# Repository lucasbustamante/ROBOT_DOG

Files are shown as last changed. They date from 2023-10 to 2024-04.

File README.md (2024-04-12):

# Robot Dog

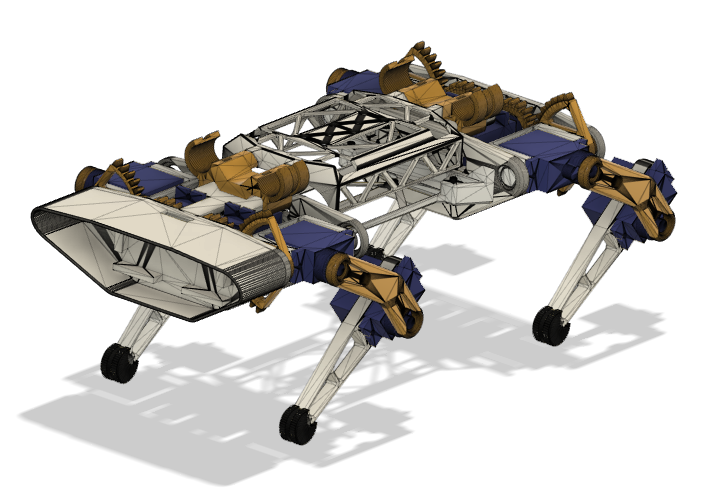
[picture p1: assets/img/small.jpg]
ROBOT_DOG


## Hardware
- ESP32
- MPU9250
- 12 servos TowerPro mg90d
- Baterias 18650
- Mini360
- INA219
- TP4056

## Software
- Compatível com Arduino IDE

## A Fazer

- [x] Criação da PCB
- [x] Alteração do Layout dos Controles
- [x] Melhorias na modelagem 3D
- [x] Impressão 3D
- [x] Montagem da Estrutura
- [x] Implementar sensor de energia INA219
- [ ] Implementar sensor de giroscópio MPU9250
- [ ] Atualizaçao das bibliotecas

## Como Fazer
### Esquema de ligação PCB

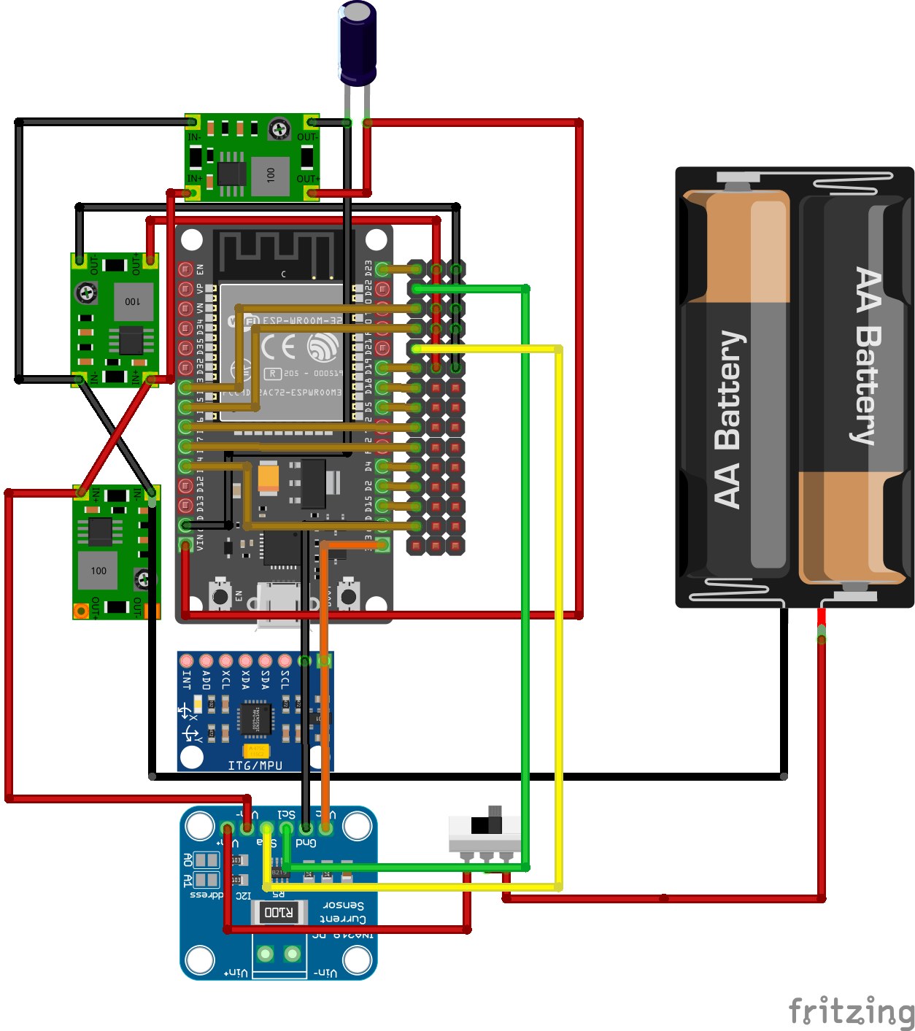
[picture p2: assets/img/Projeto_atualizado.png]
PCB


### Calibrar os servos (criar `servoMainProfile`)
- Imprima a ferramenta `calibrador do servo` e instale o servo nela: um prato circular com pontos, 10 graus cada um de 0 a 180.
- Use a ferramenta `tools/servoCalib.ino` e conecte o servo ao pino 14.
- Abra o terminal do Arduino IDE e digite `1500` (e pressione Enter) - isso deve ser o meio do servo e ele deve apontar para o ponto médio da ferramenta impressa.
- Diminua o valor para encontrar os valores `minAngle` e `degMin` (comece com `800` e diminua até o servo parar de se mover).
- Faça o mesmo para encontrar `maxAngle` e `degMax`, mas comece com 2100 e aumente os valores.
- Ótimo, agora sabemos os limites do nosso servo (ou pelo menos quais são os limites para a lib+servo), hora de encontrar posições mais precisas do servo.
- Insira valores até encontrar as posições adequadas para deg30, deg50...deg130, deg150.

### Conexão
#### Credenciais do ponto de acesso WiFi
- Renomeie config_wifi.example.h para config_wifi.h
- Mude APssid para qualquer nome do seu robô, por exemplo, SmallRobotDog
- Altere APpass para senha (8 ou mais caracteres), por exemplo MySup3rPassw0rd

- Após o upload do código para o ESP32, você poderá encontrar o SmallRobotDog WiFi com seu telefone ou tablet.
- Abra o navegador e insira o URL http://192.168.4.1/ e você verá dois joysticks virtuais para controlar o cão-robô.

### Pernas
#### Montagem
- Para montar as pernas corretamente, imprima a ferramenta `calibrador esq e dir` de calibração de perna para os ângulos Beta e Gamma, assim como a ferramenta `calibrador` de ângulo Alpha.
- Ligue o servo e conecte o ESP32 ao seu computador, abra o terminal do Arduino IDE e faça upload do código principal.
- Digite `set servo_to_calib` para definir todos os servos na posição esperada para a ferramenta de impressão.
- Monte as pernas o mais próximo possível das posições esperadas das partes da perna de acordo com a ferramenta (90 graus, 45 graus, 90 graus).

#### Calibração
- Repita os passos 2 e 3 da instrução Pernas->Montagem.
- Digite `set help` para ver a lista de comandos disponíveis, estamos interessados em `XX_HAL_trim_xxxx`, por exemplo, `LF_HAL_trim_alpha`, onde `LF` - perna frontal esquerda, e `alpha` é o nome do ângulo.
- Coloque a ferramenta de ângulo Alpha em cima dos servos das pernas do robô, a superfície da ferramenta deve estar (quase) perfeitamente alinhada com o corpo dos servos, se não estiver, use o comando `XX_HAL_trim_alpha valor_em_graus` para definir o valor de ajuste do servo, por exemplo, `set LF_HAL_trim_alpha -3`, não deve ser muito grande, em outros casos você precisa repetir o passo de Montagem.
- Usando a ferramenta para os ângulos Beta e Gamma, calibre/ajuste os outros servos.

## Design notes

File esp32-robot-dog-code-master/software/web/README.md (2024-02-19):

# Interface de Controle

## Alterar a Interface
(Este procedimento foi testado apenas em sistemas Linux)

Para alterar a interface de controle, siga as etapas abaixo:

1. Localize o arquivo **index.html** no seguinte caminho: `/esp32-robot-dog-code-master/software/web/src`.

2. Após efetuar as alterações necessárias, você precisará converter este arquivo HTML para os formatos **.gz** e **.gz.h**.

3. Agora, abra o terminal e navegue até o seguinte caminho: `/esp32-robot-dog-code-master/software/web`.

4. Execute os seguintes comandos:
   (use a versão 12 ou inferior do Node.js)
   - `npm install`: Isso instalará os pacotes do Node.js necessários.
   - `gulp`: Este comando irá compilar a interface web.

5. O arquivo resultante estará disponível na pasta **web** do projeto.

Agora você concluiu o processo de geração da nova interface com sucesso.

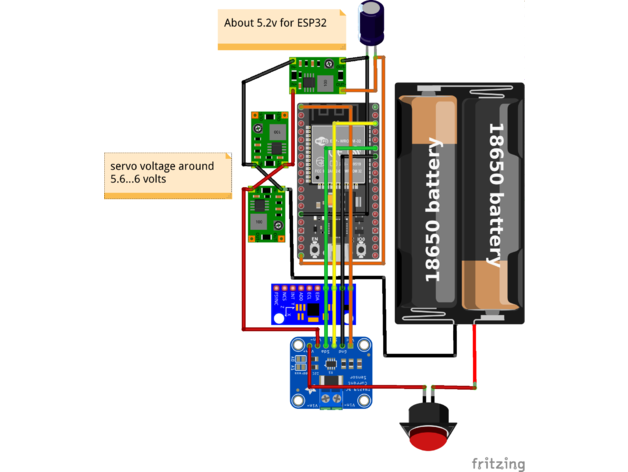
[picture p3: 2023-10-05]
Modelo 3D/images/featured_preview_scheme_power_and_sensors.png

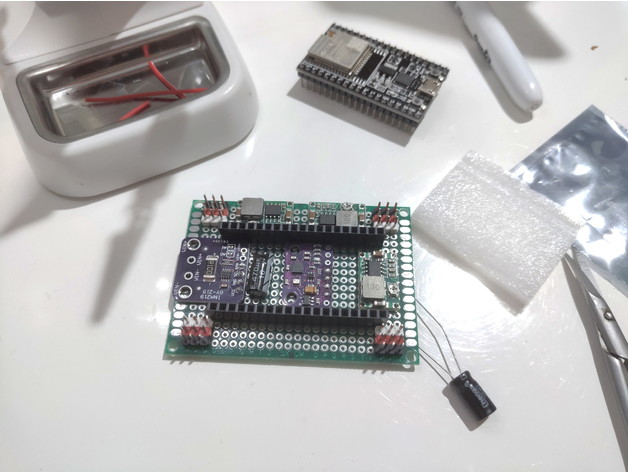
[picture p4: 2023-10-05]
Modelo 3D/images/featured_preview_2021-03-04_20.57.48.jpg

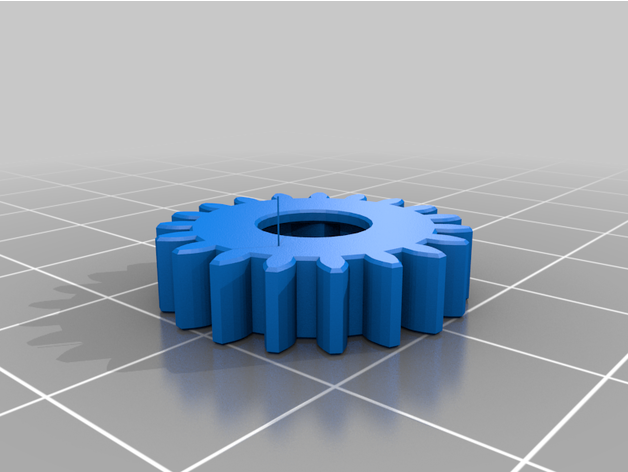
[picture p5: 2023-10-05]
Modelo 3D/images/servo_gear.png

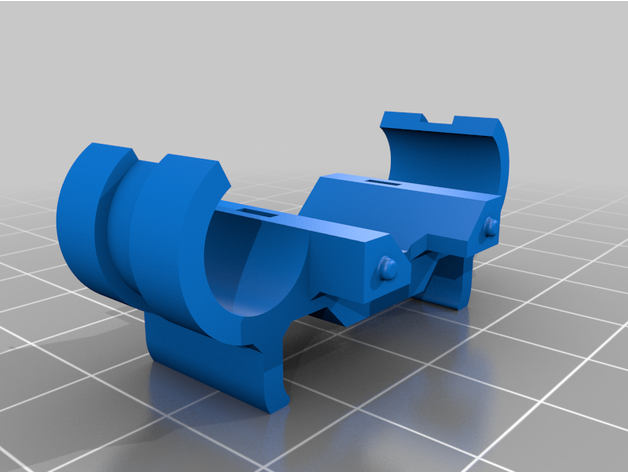
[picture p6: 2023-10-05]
Modelo 3D/images/cover_clamp.png

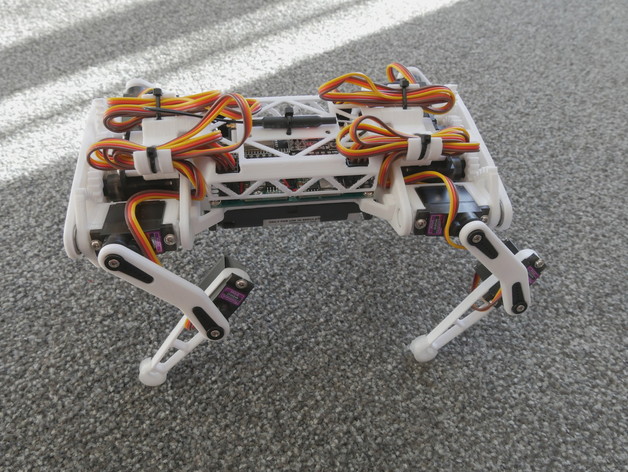
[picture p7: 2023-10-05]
Modelo 3D/images/featured_preview_2.JPG

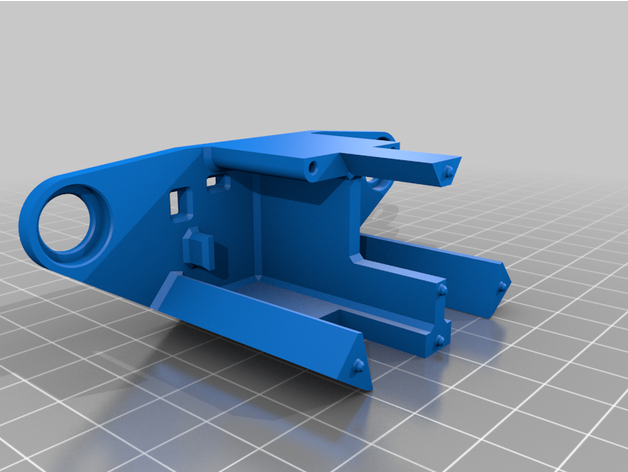
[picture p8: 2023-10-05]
Modelo 3D/images/legs_holder_part1.png

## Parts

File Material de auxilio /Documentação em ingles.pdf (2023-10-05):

instructables

## ESP32 Small Robot Dog (closed) (http://www.instructables.com/ESP32-Small-Robot-Dog/)

by Gleb Devyatkin (http://www.instructables.com/member/Gleb+Devyatkin/)

### Disclaimer

This project has been done mostly for fun about a year ago. Some libraries have been updated, so it basically does not work any more. Not every planned feature was released. No PCB is made and it creates a lot of trouble for most of you. I'm sorry to say, but I'm not going to provide any support for it any more. It's exhausting and sometimes just destroys any intentions to continue. This is not commercial project and I'm not going to do something like Donation. Maybe I'm disappointing someone. Sorry. Project closed.

ESP32 small robot dog is my attempt to make quadruped dog that become very popular after Boston Dynamics Spot. Work on the project still in progress and hardware and software can changed.

### Features

### Only ESP32 required (you don't need additional PWM i2c, Bluetooth modules, etc) Arduino IDE

Web based interface with telemetry, to control robot you will need just you smartphone or tablet

### CLI interface for calibration and debug True Inverse kinematics code Con0gurable Gait sequence and settings (just if you need it) Fun

### Electronics

### 1 x ESP32 with 38pin 1 x 50x70 mm green prototyping board

12 x TowerPro MG90D or MD90S (cable should be out at the bottom of servo, thanks to triawan) (https://www.thingiverse.com/make:942053) servos (it can be tricky to use other servos, as size may vary, please have a look at this images of three di9erent

### mg90-like servos: https://www.instagram.com/p/COoIyvzrLZt/) 1 x INA219 (optional) 1 x MPU9250 (optional, still has not been implemented, WIP)

3 x Mini360 (DC-DC Buck Converter Step Down Module) or similar, 2 for front/hind legs (or more), 1 for

### ESP32 1 x 18650 Battery Holder for 2 elements (try to 0nd "18650 battery holder smt") 2 x 18650 Battery some capacitors

### Other parts

ESP32 Small Robot Dog (closed): Page 1

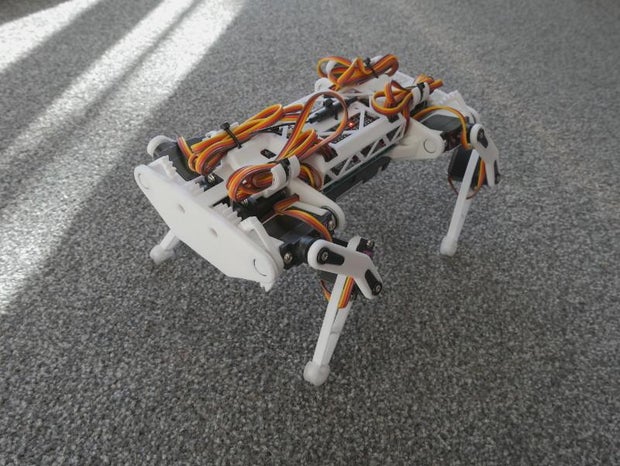
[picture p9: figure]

Step 1: Print Parts

### 8 x 8x12x2.5mm bearings 4 x small cable ties Super glue (cyanoacrylate) to glue all parts together

https://www.youtube.com/watch?v=jzs04zd9bQk

All STLs to print can be downloaded from Thingiverse page: Robot dog, quadruped robot, 12DOF, 3DOF per leg (https://www.thingiverse.com/thing:4822059)
Some part should be mirrored to be able to print correctly. Please see attached images.
My printer have issue with 0rst layer thickness, aka Elephant Foot. Gears should be printed as perfect as possible, so I add very tiny spacer to avoid issue, you will see that some part "Eying" over surface, so please enable support for it.
I'm strongly recommend print parts with best possible quality, especially gears. As also use brim and ironing.

### Full list of parts to print: Printable parts: 1 x Body

### 2 x Leg top 2 x Leg top (mirrored) 2 x Leg bottom 2 x Leg bottom (mirrored) 4 x Shoulder part1 4 x Shoulder part2 2 x Legs holder part1 2 x Legs holder part2 4 x Servo gear 4 x Leg shoes, print with Eexible 0lament (not required) 1 x Cover 2 x Cover clamps

Printable helping tools (see description on GitHub): (https://github.com/SovGVD/esp32-robot-dog-code)

### 1. 1 x CALIBRATION_LEG-Beta_and_Gamma 2. 1 x CALIBRATION_LEG-Beta_and_Gamma (mirrored) 3. 1 x CALIBRATION_LEG-Alpha 4. 1 x CALIBRATION_SERVO-10deg

I'm using Ender 3 Pro, Cura, use Support and choose Dynamic quality. Plastic is PLA from OPY (AliExpress). For more

### details please visit Thingiverse page: https://www.thingiverse.com/thing:4822059

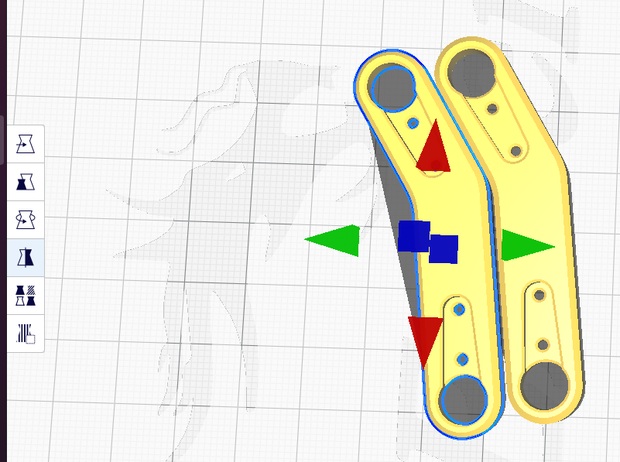
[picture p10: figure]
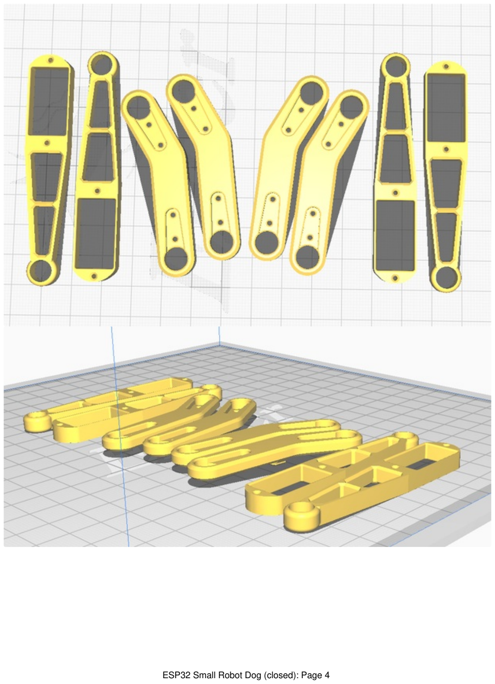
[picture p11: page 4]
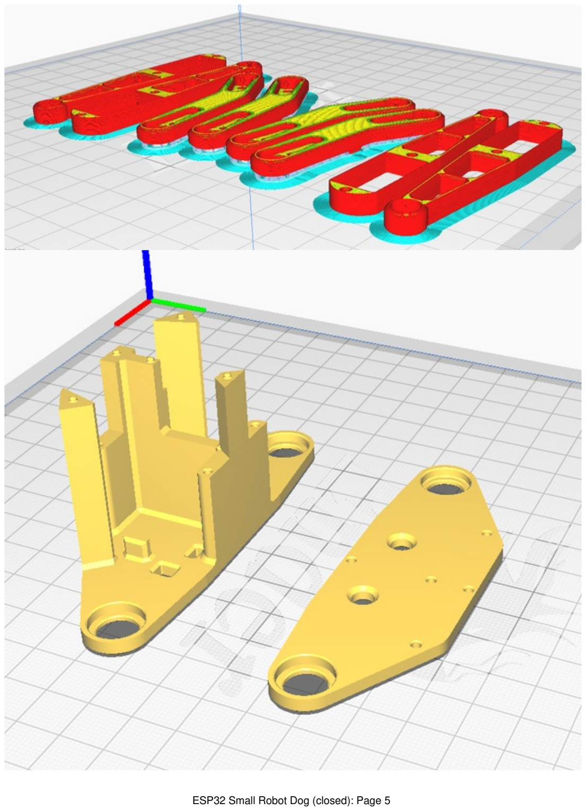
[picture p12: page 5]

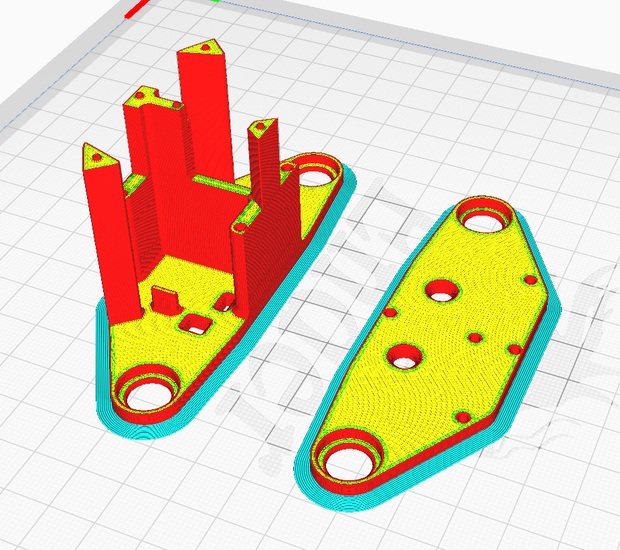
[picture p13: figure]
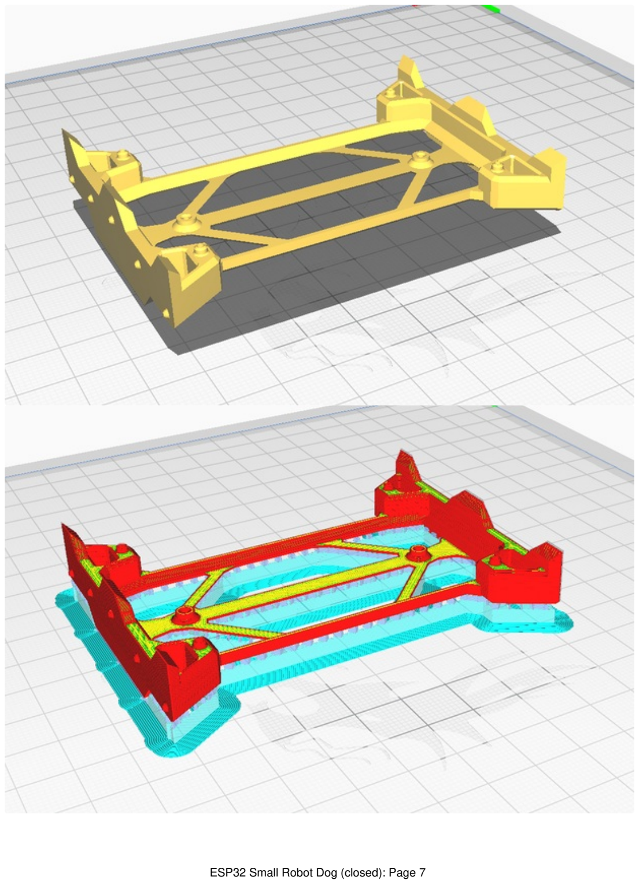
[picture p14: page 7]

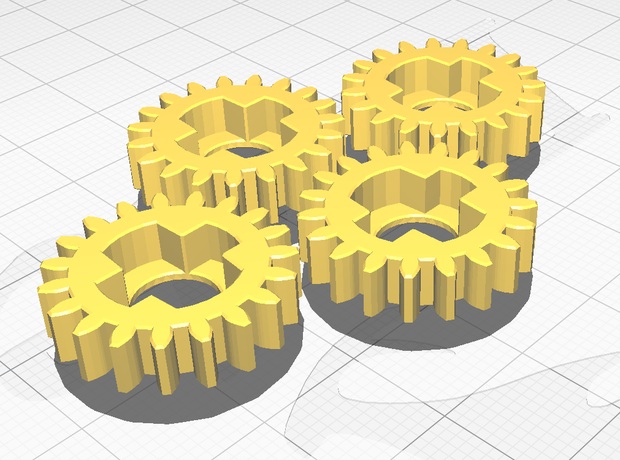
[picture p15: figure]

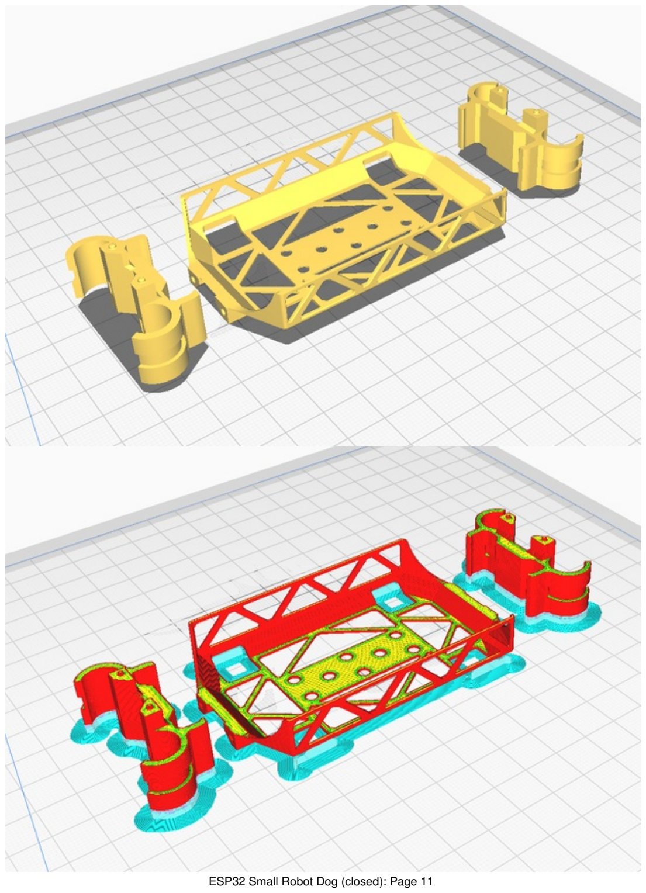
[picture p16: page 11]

Step 2: Let's Make It Better and Glue Together

### Preparation

Before we start, please check that bearings can be easy 0t to body parts and over shoulder parts.
Also check that holes in Shoulder and body parts printed 0ne and servo cables (temporary disassemble servo connector) can be 0t inside.

### Do it

I tried to make body as light as possible, as small servos not very powerful. That is why you will need to glue some parts

### together. Promise it is not so hard =)

Make sure that gluing surfaces are Eat, use some Eat mini 0le and make sure parts can be connected to each other without space between. Then glue it together as shown on images.

### Servo gears

Cut servo horn (see image) to 0t it inside servo gear part and glue it together.





Step 3: Legs

Glue short servo horns into "leg top" parts.
Insert servo into "leg bottom part" and insert cable as shown on image. Pull another servo cable through one of the hole on the "shoulder" part. Repeat with other legs.





Step 4: Assemble Body and Legs Together

As was shown on previous pictures, pull all cables through legs and body holes.
Set all servos to middle using Arduino/ESP32 or servo tester.
Cut servo horn to make it 0t inside "servo gear", glue it and install on the servo as usual. Insert servos into body. Screwing it can be challenging.
Squeeze "shoulder" part without servo (but with cable in place) and insert it between bearings.
Repeat with other servos and parts.
You don't need to 0x legs with bolts at that moment, later you will need to calibrate legs following instruction in my

### GitHub repository: https://github.com/SovGVD/esp32-robot-dog-code





Step 5: PCB

PCB con0guration is up to you. I can only show what I did. Sensors connected to default I2C bus of ESP32 (GPIO 21 and 22).

### Servos connected to:

Left front: 25 (body servo, servo gear, alpha), 26 (body to leg servo, shoulder, beta), 27 (leg servo,gamma)

### Right front: 16, 18, 17 Left hind (back): 13, 12, 14 Right hind (back): 4, 2, 15

You can recon0gure it in the code, but make sure that ESP32 ISR Servo library (https://github.com/khoih-prog/ESP32_ISR_Servo/) support it.





Thank you for all the effort you put into this. I built it but I did have problems soldering up the board, as others did apparently, so I decided to create a pcb instead. If you reboot this project and would like me to upload my gerber files let me know.

I would definitely appreciate some PCB files being posted- I tried soldering one up but my parts aren't exactly the same as his so the arrangement is different, so my pcb is a mess of wires and is extremely difficult to troubleshoot. Thanks in advance!

I also had a heck of time wiring up the circuit. I thought it was me but apparently others have also found it quite challenging. After two failed attempts at laying out and soldering up the board I decided to try creating a pcb using Fritzing. I did it and sent it out to Aisler to be printed. The board looks good but I haven't tried to use it so I can't say if it actually works or not. Unfortunately it seems I'm not allowed to updoad zip files or the gerber file types so I've uploaded my Fritzing circuit file and a pdf of it. Good luck!

Thanks! I ended up designing my own PCB based on the schematic since I wanted to use the IMU, but I appreciate the help. Fritzing’s autoroute feature really is a lifesaver.

Perfect!

Step 6: Code
Step 7: Good Luck!

Setup Arduino IDE to work with ESP32 (https://randomnerdtutorials.com/installing-the-esp32-board-in-arduino-ide-windows-instructions/) but don't use esp32 version 2 and higher. There were some strange changes

### related to WiFi, so one of the core just freezing in v2.x.x

Install addition libraries (most of them could be installed in Arduino IDE "Sketch" menu -> "Include Library" -> "Manage

### Libraries...", please use only specied version):

ESP Async Web Server (https://github.com/me-no-dev/ESPAsyncWebServer) with Async TCP (https://github.com/me-no-dev/AsyncTCP) ESP32 ISR Servo (https://github.com/khoih-prog/ESP32_ISR_Servo#use-arduino-library-manager) version 1.1.0

### MPU9250_WE (https://github.com/wollewald/MPU9250_WE) version 1.1.3 INA219_WE (https://github.com/wollewald/INA219_WE)

Setup WiFi Access point credentials.

### 1. Rename con0g_wi0.example.h to con0g_wi0.h 2. Change APssid to any name of your robot, e.g. SmallRobotDog 3. Change APpass to password (8 or more chars), e.g. MySup3rPassw0rd

4. After code upload to ESP32 you should be able to 0nd SmallRobotDog WiFi with your phone or tablet.

Open browser and input URL http://192.168.4.1/ and you will see two virtual joystick to control robot dog.

Hope you like that project. More code and instruction updates on the go and hopefully will be release soon.

I try to compile the code you give but at the end is Hal_PWM is error the arduine IDE wont finish its compile before insert code to Esp32. Any idea how to solve it?

Hi. I just tried this code with newest version of all libraries and found that everything broken =( I've update instruction with versions that at least should compile without errors:
- ESP32 ISR Servo version 1.1.0
- MPU9250_WE version 1.1.3
Version of the library could be chosen in Arduino IDE Library manager in dropdown menu near Install button.
I will try to update code and test it with latest version of library some times later (with the new walking robot). Sorry, just have no time at the moment for that project and did not see anyone going to help with it.

That Library is Good to go. If you want help from me i can help you but I dont know how to start with, im newbie. Now I'm going to build the circuit board. In time I try to connect with My Computer browser it does show up 2 button to control the robot but when I try to using My phone its show the button but can't shake it. I don't know why?

Try another browser. I'm using Android phone with Google Chrome.

goggle browser is now work, the button can move but after Wifi connect to robot when i try to move the button nothing happen. what should i do next?

Did you assemble robot, connect all servos and provide power to it?

Yes I already assemble it.
and power it. All servo had rotation.

I think its lack in my Component, i don't use MPU and INA219 I only power it straight to Esp and servo. Maybe that the reason why it can't move. (The article above is Optional)

MPU and INA should not be the problem. Sorry but I can't test my setup without that sensors. As also can't check code at the moment. Maybe this weekend I will find time for it.

Dear Mr. Gleb
Sorry to bore you, i think I will use Ina and Mpu next. but I already Solve it, it seem my Esp32 Core is corrupted so I Re-Install the library, its work like charm. But when I turn on the Robot all Servo move like crazy, its seems the Servo Pin is not correct, like Pin 16 in Esp32 I cant find the Pin.
I would know all Pin did you use for Servo?

Dear Mr. Gleb
I already figure out about ServoPin, now the robot can move correctly but when I turn on the esp and servo with power, all servo move clockwise and temporary i build 2 switch, 1 for esp and 2 for servo. it seems when power up esp and servo together esp had low voltage and reset the positioning servo but after a few second servo go back to original position. how do you solve this problem?
I too put some capasitor but it does nothing, by the way I use 330uf,
what capacitor did you use?
well another problem to solve

Best Rigard

Hi. You are not the first who have that problem and I can't reproduce it to understand and fix. I'm using mg90d servos.

I will check the Mg90d servo although i use Mg90s,
i think the problem is on trimmer setting on first boot, it say :
0 leg trim (0,0,0)

1 leg trim (0,0,0)
2 leg trim
3 leg trim
but when we find place where to adjust, the problem will solve.
need time to learn,

Hi, great design, thanks! One question about the servos, you say MG90D or MG90S, will the MG90S fit properly? Someone on Instagram said it didn't fit.

its Fit for Mg90s Servo. I try it already.
if not in 3D setting or Printer type the tolerrance is big.

Hi i saw in photos that you connect something to vin+ and vin- but you didnt show in pcb layout

Hi, ina219 module have 2 pairs of vin+ and vin-. On scheme it is connected to pins near i2c data pins.

To ina 219

İf you cant find ESP Async Web Server in arduino libraries you should download this libraries to arduino https://github.com/me-no-dev/ESPAsyncTCPhttps://github.com/me-no-dev/ESPAsyncWebServer
these two libraries literally solve my problems. Thanks to Gleb Devyatkin

Yes, that two, sorry for delay with reply. I add links to libraries.

hello sir

Hello

how did you connect the inner servos to the gears? i dont see that in your instructions. Please assist. Thank you

Updated. You need to cut one of the servo horns to make it fit inside printed gear. Use glue.

Thanks thats what I thought but just wanted to be certain.

Am I missing the PCB layout? Please post it too or a link on how to put all the electronics togeter.

In step 5 you can find scheme of connection for most of parts, as also list of pins for servos. It is not properly made PCB, just connections.

What is the spec for the capacitor and what is it for?

I think it's not required for that project. I used to use a couple of capacitors in another project, where start of DC motor take too much power for a very short period of time, so capacitor save controller from poweroff at the start.

well, its in your photos and on the drawing. therefore I was asking.

Looks cool. Can it already walk too?

It can walk.

This looks amazing! How much is the estimated cost of parts? Except the 3D printer of course.

Sorry, I did not count the final cost. And it will be very different depends on shops with electronic parts or delivery price. Everything (including fillament for 3D printer) bought on Aliexpress.

Well this looks totally amazing, well done. I hope you continue developing it. I'm amazed how good it is with standard small servos. Maybe next one will be bigger and use stepper motors now you've proved the concept.

Thank you. New features in progress. I made this small robot dog to easy test code and algorithms for the bigger version (also servo based): https://www.instagram.com/p/CDX-HhODbw4/ (https://www.instagram.com/p/CDX-HhODbw4/)

amazing!

Awesome!

Very nice work! : )

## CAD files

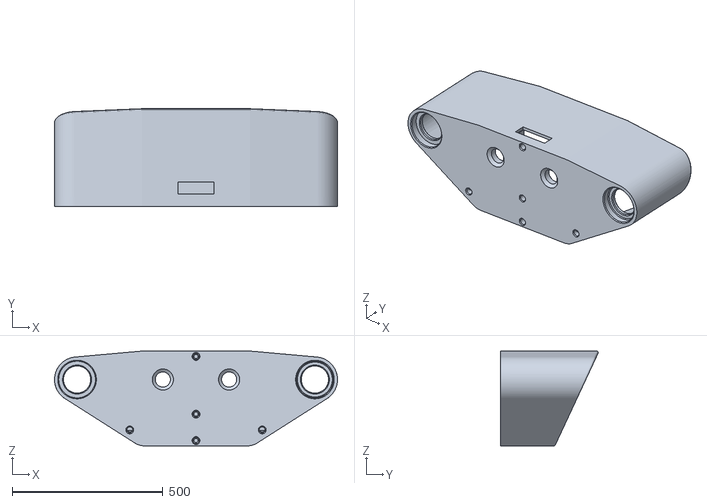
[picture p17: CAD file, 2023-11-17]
Modelo 3D/files/suporte perna part2 v1.stl
940.0 x 324.1 x 315.1

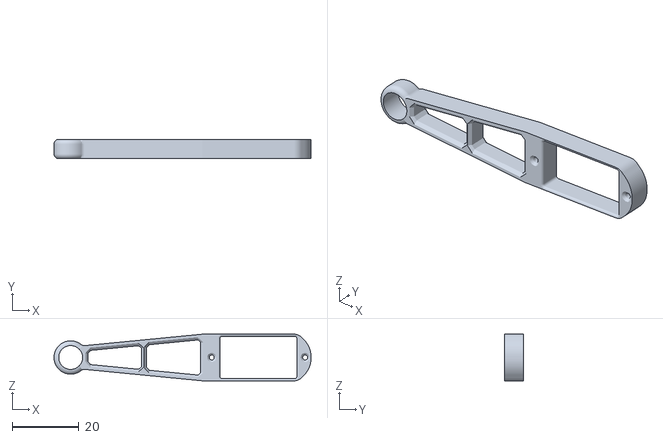
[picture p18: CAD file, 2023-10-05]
Modelo 3D/files/pata.stl
77.0 x 5.80 x 14.0

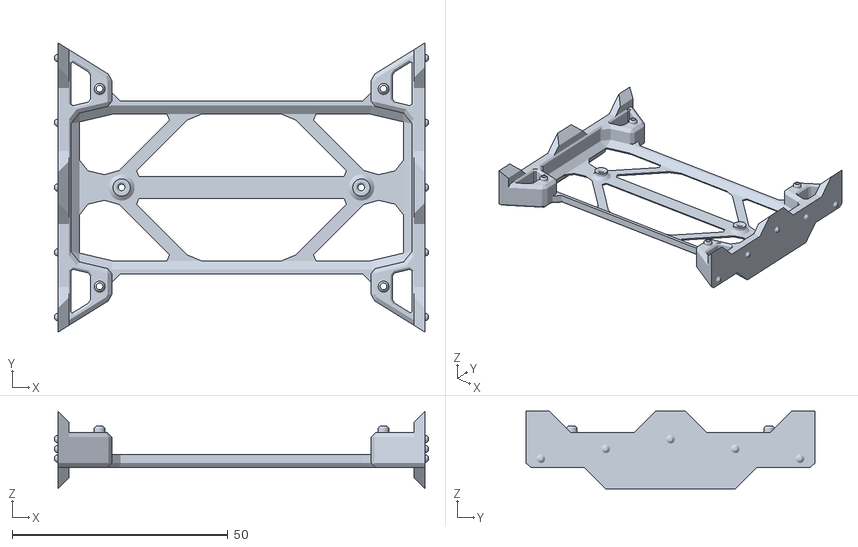
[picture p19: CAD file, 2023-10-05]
Modelo 3D/files/corpo.stl
86.6 x 67.0 x 18.0

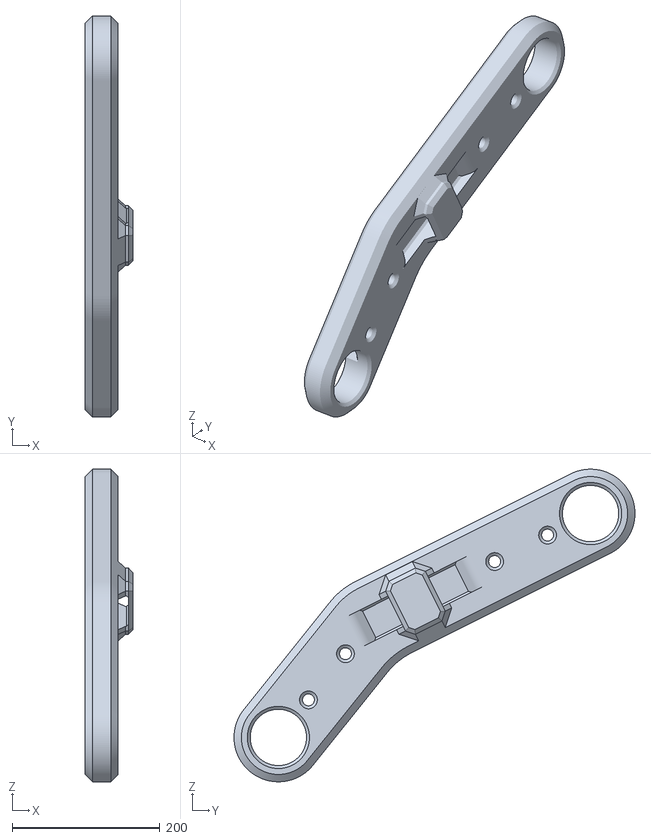
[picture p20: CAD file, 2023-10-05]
Modelo 3D/files/perna dir.stl
65.0 x 541.9 x 422.6

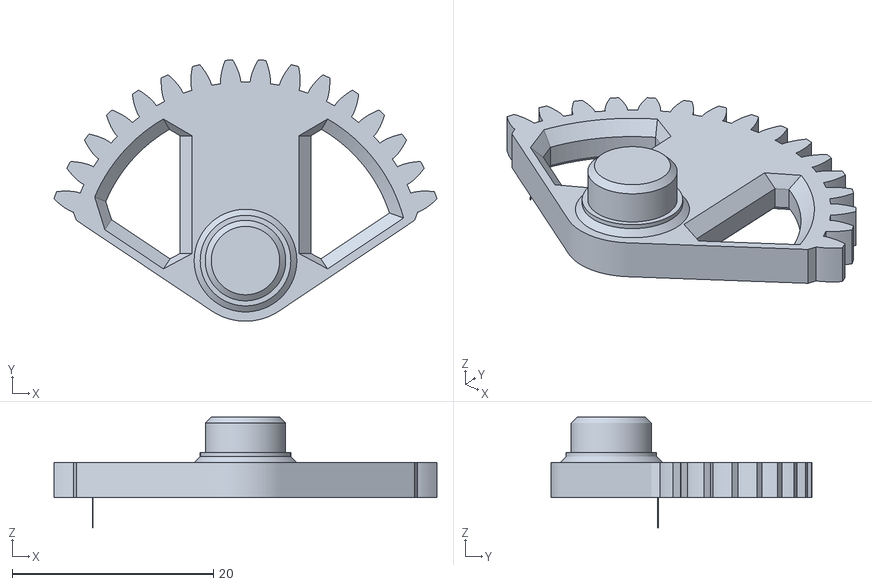
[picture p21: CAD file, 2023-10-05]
Modelo 3D/files/ombro part1.stl
38.1 x 26.0 x 11.0

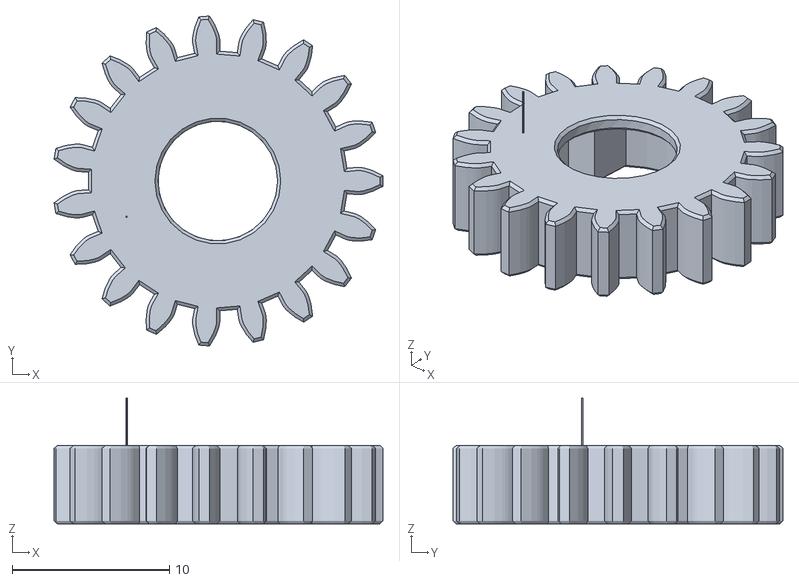
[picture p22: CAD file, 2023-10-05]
Modelo 3D/files/engrenagem servo.stl
20.9 x 21.0 x 8.00

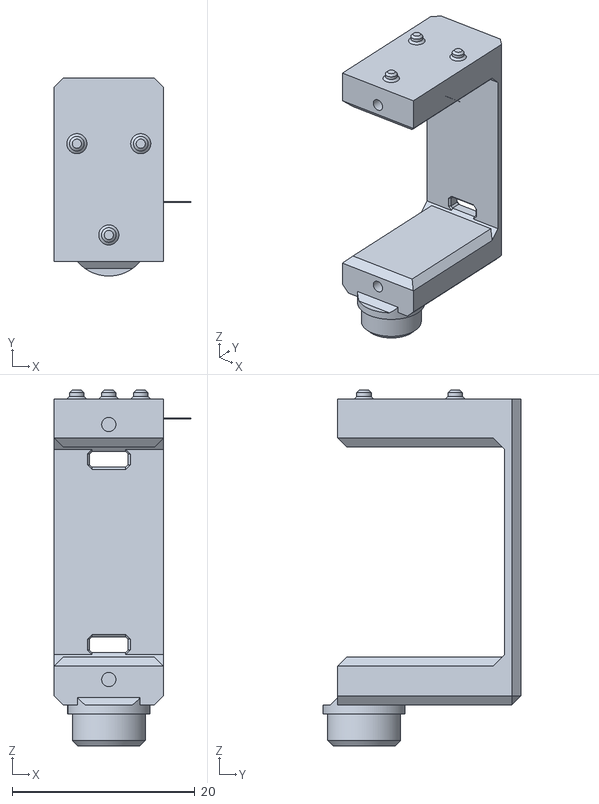
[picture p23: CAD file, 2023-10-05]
Modelo 3D/files/ombro part2.stl
15.0 x 21.7 x 39.0

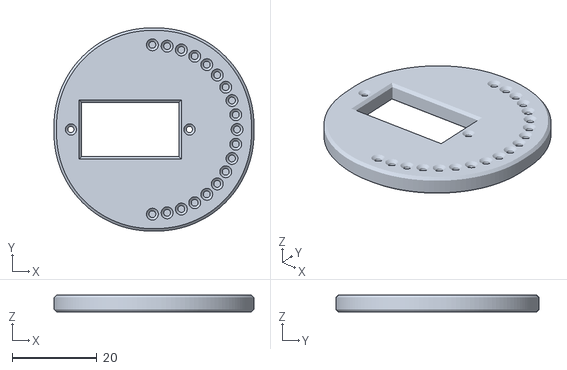
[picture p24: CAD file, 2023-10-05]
Modelo 3D/files/calibrador do servo.stl
47.2 x 48.0 x 4.00

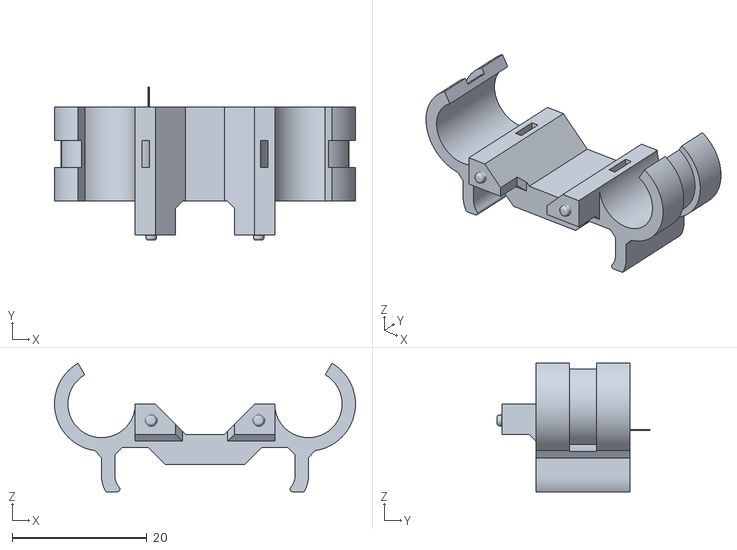
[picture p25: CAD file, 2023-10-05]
Modelo 3D/files/presilhas.stl
44.7 x 22.8 x 19.1

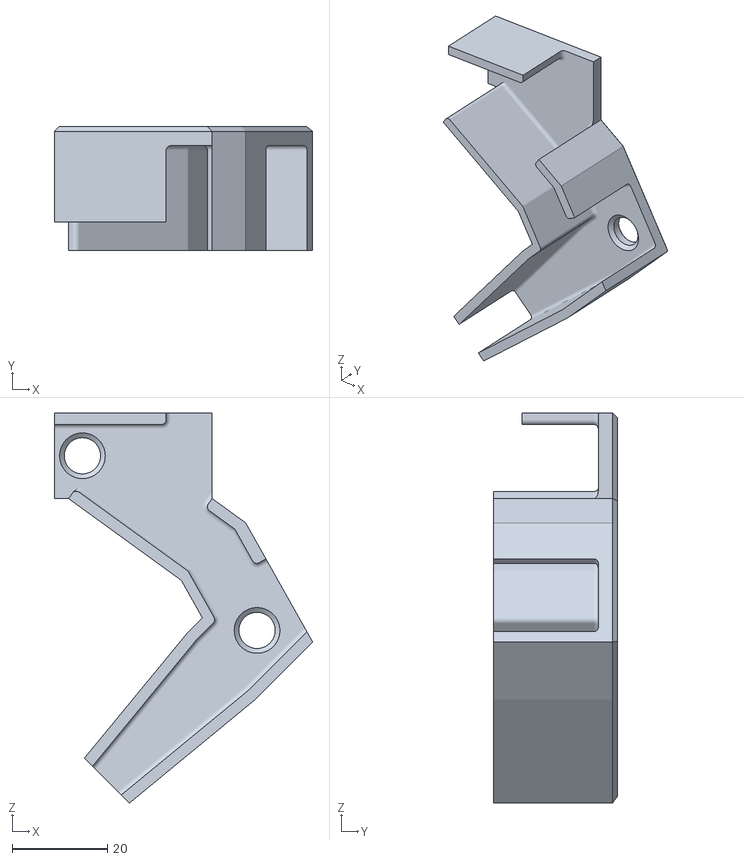
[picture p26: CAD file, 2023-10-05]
Modelo 3D/files/calibrador esq.stl
54.3 x 26.0 x 82.0

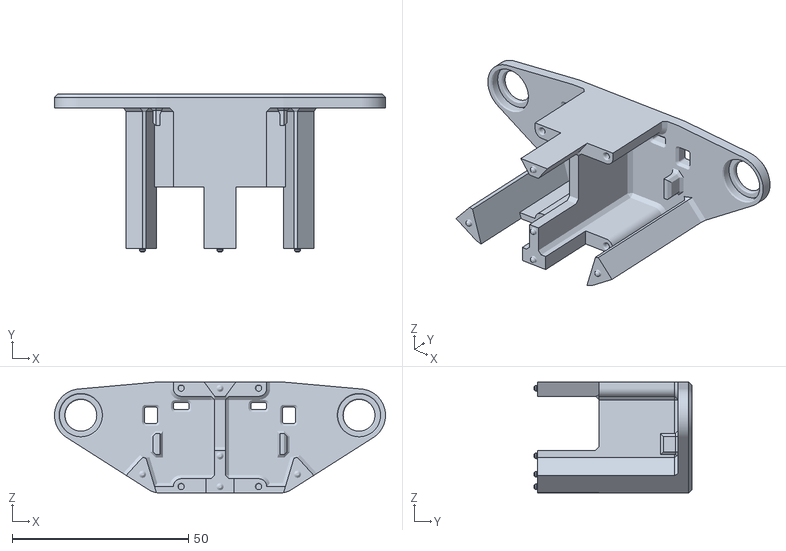
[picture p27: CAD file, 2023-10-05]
Modelo 3D/files/suporte perna part1.stl
94.0 x 45.0 x 31.5

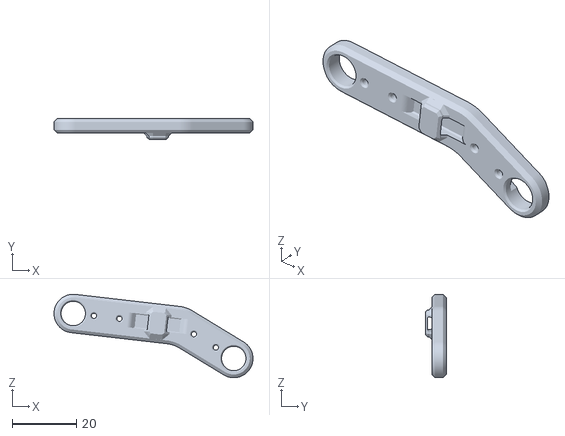
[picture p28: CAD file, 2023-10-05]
Modelo 3D/files/perna esq.stl
62.0 x 6.50 x 26.0

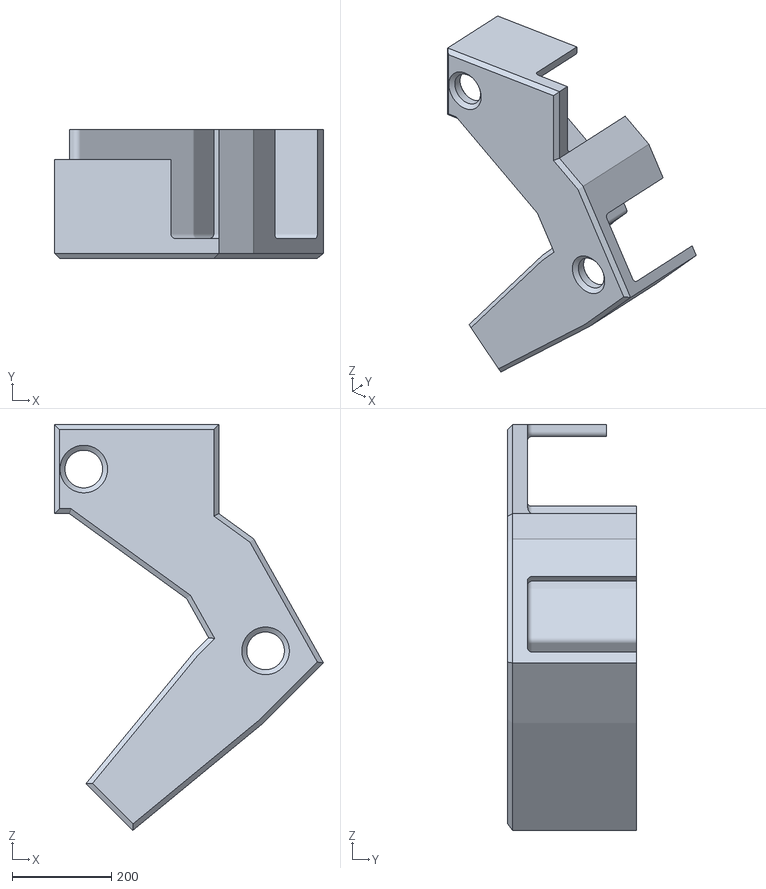
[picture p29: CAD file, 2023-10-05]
Modelo 3D/files/calibrador dir.stl
543.3 x 260.0 x 820.0

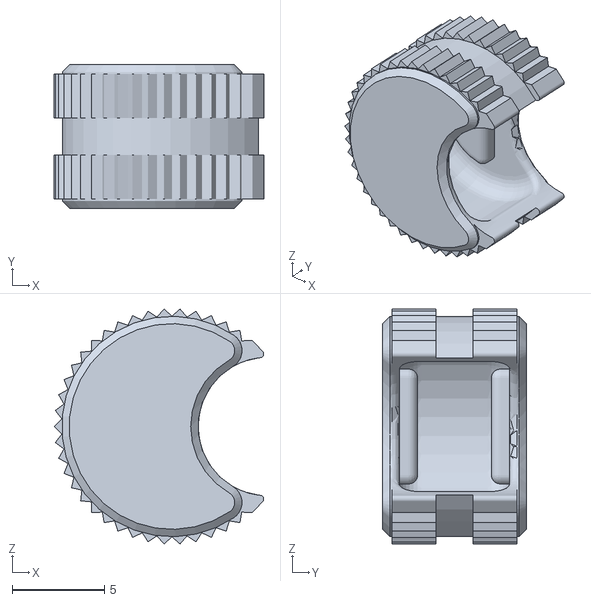
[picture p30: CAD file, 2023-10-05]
Modelo 3D/files/pé anti derrapante.stl
11.4 x 7.80 x 12.8

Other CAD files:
Modelo 3D/files/calibrador.stl
Modelo 3D/files/suporte perna on_off.stl
Modelo 3D/files/suporte perna part2.stl

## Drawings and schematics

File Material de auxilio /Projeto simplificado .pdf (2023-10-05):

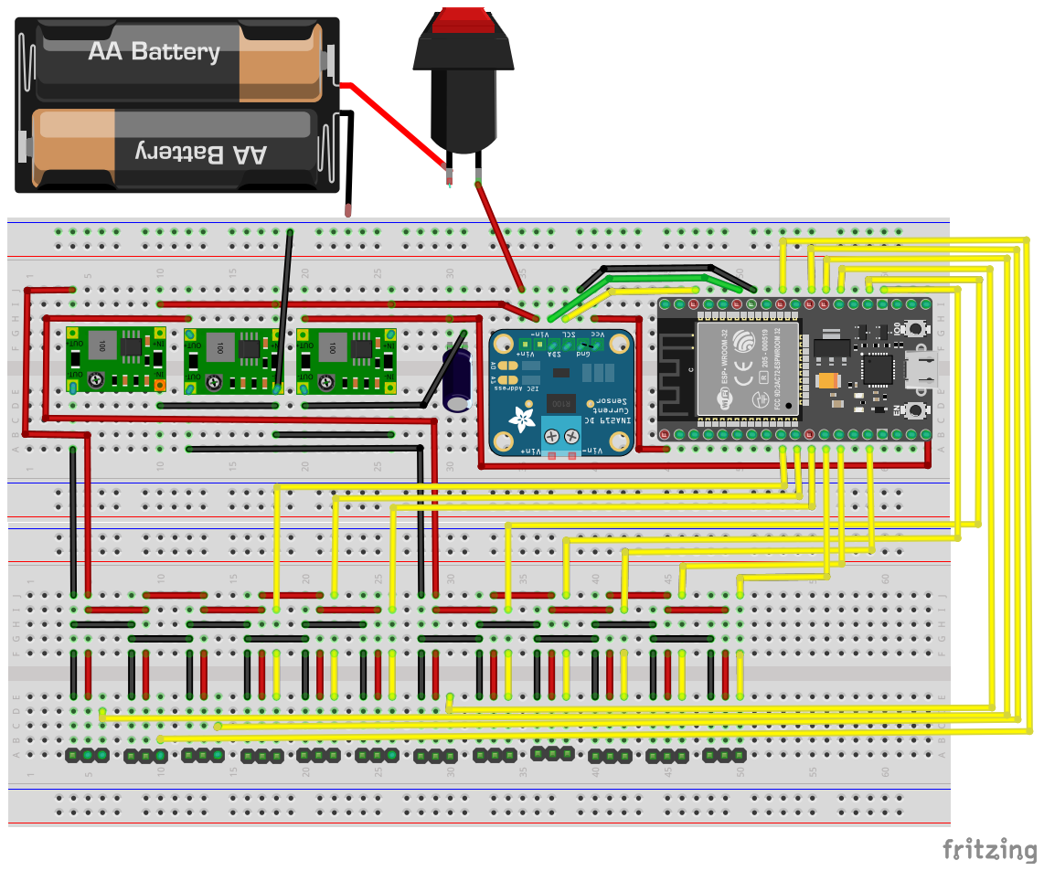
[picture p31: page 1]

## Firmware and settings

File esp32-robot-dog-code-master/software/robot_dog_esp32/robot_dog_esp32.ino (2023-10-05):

#include <math.h>

#include "libs/IK/geometry.h"
#include "libs/IK/leg.h"
#include "def.h"
#include "config.h"
#include "config_small.h"
#include "config_wifi.h"
#include "libs/IK/IK_simple.h"  // TODO this is for small dog only!!!
#include "libs/planner/planner.h"
#include "libs/balance/balance.h"
#include "libs/gait/gait.h"
#include "libs/HAL_body/HAL_body.h"

#include <EEPROM.h>
#include "WiFi.h"
#include <ESPAsyncWebServer.h>
#include "web/index.html.gz.h"
#include "cli.h"
#include "subscription.h"

#include <MPU9250_WE.h>
#include <Wire.h>

#include "libs/IK/IK_simple.cpp"  // TODO this is for small dog only!!!
#include "libs/planner/planner.cpp"
#include "libs/balance/balance.cpp"
#include "libs/gait/gait.cpp"
#include "libs/HAL_body/HAL_body.cpp"

/**
 * Hardware libraries
 */
#if PWM_CONTROLLER_TYPE == PCA9685
  #include <Adafruit_PWMServoDriver.h>
#endif

#if PWM_CONTROLLER_TYPE == ESP32PWM
  #define USE_ESP32_TIMER_NO 3
  #include "ESP32_ISR_Servo.h"
#endif

#ifdef POWER_SENSOR
  float voltage_V = 0.0;
  float current_A = 0.0;

  #if POWER_SENSOR == INA219
    #include <INA219_WE.h>
    INA219_WE ina219;
  #endif
#endif

float IMU_DATA[3] = {0, 0, 0};
MPU9250_WE IMU;

// run commands on diferent cores (FAST for main, SLOW for services)
bool runCommandFASTCore = false;
bool runCommandSLOWCore = false;
cliFunction cliFunctionFAST;
cliFunction cliFunctionSLOW;
double cliFunctionFASTVar = 0.0;
double cliFunctionSLOWVar = 0.0;

TaskHandle_t ServicesTask;

#if PWM_CONTROLLER_TYPE == PCA9685
  Adafruit_PWMServoDriver pwm;
#endif

unsigned long currentTime;
unsigned long previousTime;
unsigned long loopTime;

unsigned long serviceCurrentTime;

unsigned long servicePreviousTime;
unsigned long serviceLoopTime;

unsigned long serviceFastPreviousTime;
unsigned long serviceFastLoopTime;

bool HALEnabled = true;

// Gait
uint16_t ticksPerGaitItem    = 0;
uint16_t ticksToNextGaitItem = 0;
uint8_t  currentGait         = 0;
uint8_t  nextGait            = 0;
double   gaitItemProgress    = 0;
double   gaitProgress[]      = {0, 0, 0, 0};

transition bodyTransition;
transitionParameters bodyTransitionParams = {{0,0,0}, {0,0,0}, 0};

//Move
moveVector vector = {
  {0, 0, 0},
  {0, 0, 0}
};

//Failsafe
bool FS_FAIL = false;
uint8_t FS_WS_count = 0;

// HAL
figure body = {
  {  0,  0,  0},
  {  0,  0,  0}
};

IK ikLegLF(legs[LEGLF], body);
IK ikLegRF(legs[LEGRF], body);
IK ikLegLH(legs[LEGLH], body);
IK ikLegRH(legs[LEGRH], body);

/* We need predict future position of legs/body */
planner walkPlanner(
  vector,
  body,
  legs[LEGLF],
  legs[LEGRF],
  legs[LEGLH],
  legs[LEGRH]
);

/* and balance it someway */
balance bodyBalance(
  balanceOffset,
  body,
  legs[LEGLF],
  legs[LEGRF],
  legs[LEGLH],
  legs[LEGRH]
);

HAL_body bodyUpdate(vector, body, legs);

// WebServer
bool clientOnline = false;
int WiFiMode = AP_MODE;
IPAddress WiFiIP;
AsyncWebServer server(80);
AsyncWebSocket ws("/ws");
uint8_t telemetryPackage[P_TELEMETRY_LEN];

// CLI
Stream *cliSerial;

// Subscriptions
bool subscriptionEnabled = false;
bool subscriptionBinary = false;

bool mainLoopReady = false;
bool serviceLoopReady = false;


void setup()
{
  Serial.begin(SERIAL_BAUD);
  delay(100);

  initSettings();
  delay(100);
  
  initHAL();
  delay(100);
  
  initGait();
  delay(100);
  
  xTaskCreatePinnedToCore(
    servicesLoop,   /* Task function. */
    "Services",     /* name of task. */
    100000,         /* Stack size of task */
    NULL,           /* parameter of the task */
    1,              /* priority of the task */
    &ServicesTask,  /* Task handle to keep track of created task */
    0);             /* pin task to core 0 */

  mainLoopReady = true;
}

/**
   Main loop for all major things
   Core 1
*/
void loop()
{
  currentTime = micros();
  if (mainLoopReady && serviceLoopReady && currentTime - previousTime >= LOOP_TIME) {
    previousTime = currentTime;

    updateFailsafe();
    updateGait();
    updateHAL();
    doHAL();

    FS_WS_count++;

    loopTime = micros() - currentTime;
    if (loopTime > LOOP_TIME) {
      Serial.print("WARNING! Increase LOOP_TIME: ");
      Serial.println(loopTime);
    }
  }
}

/**
   Loop for service things, like CLI
   Core 0
*/
void servicesSetup() {
  cliSerial = &Serial;
  initCLI();
  initSubscription();
  Wire.begin();
  Wire.setClock(400000);
  delay(100);

  initIMU();
  delay(100);

  initPowerSensor();
  delay(100);

  initWiFi();
  delay(100);
  
  initWebServer();
  delay(100);

  serviceLoopReady = true;
}

void servicesLoop(void * pvParameters) {
  servicesSetup();

  while(mainLoopReady && serviceLoopReady) {
    serviceCurrentTime = micros();

    if (serviceCurrentTime - serviceFastPreviousTime >= SERVICE_FAST_LOOP_TIME) {
      serviceFastPreviousTime = serviceCurrentTime;

      updateIMU();
      
      runFASTCommand();
      doFASTSubscription();

      serviceFastLoopTime = micros() - serviceCurrentTime;
      if (serviceFastLoopTime > LOOP_TIME) {
        Serial.print("WARNING! Increase SERVICE_FAST_LOOP_TIME: ");
        Serial.println(serviceFastLoopTime);
      }      
    }

    if (serviceCurrentTime - servicePreviousTime >= SERVICE_LOOP_TIME) {
      servicePreviousTime = serviceCurrentTime;

      updateWiFi();
      updatePower();
      runSLOWCommand();
      updateCLI();
      doSLOWSubscription();

      serviceLoopTime = micros() - serviceCurrentTime;  // this loop + service fast loop
      if (serviceLoopTime > LOOP_TIME) {
        Serial.print("WARNING! Increase SERVICE_LOOP_TIME: ");
        Serial.println(serviceLoopTime);
      }

    }
    vTaskDelay(1);  // https://github.com/espressif/arduino-esp32/issues/595
  }
}

void runFASTCommand()
{
  if (runCommandFASTCore) {
    runCommandFASTCore = false;
    cliFunctionFAST(cliFunctionFASTVar);
  }
}

void runSLOWCommand()
{
  if (runCommandSLOWCore) {
    runCommandSLOWCore = false;
    cliFunctionSLOW(cliFunctionSLOWVar);
  }
}

/**
   TODO
    - calculate center of mass and use it for balance
    - make the queue of tasks by core, e.g. not just   cliFunctionFAST = runI2CScanFAST; but array/list with commands
    - i2c pwm broken, i2c in service loop

*/

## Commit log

2023-10-10 update stl
2023-10-14 update esquema pcb e html
2023-10-27 servo pins update
2023-11-13 assets update
    [Untitled Sketch 8.fzz]
